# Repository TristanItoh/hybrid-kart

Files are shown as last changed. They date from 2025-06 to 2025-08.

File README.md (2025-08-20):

# The Hybrid Truck Kart
A custom hybrid truck-style go-kart with a 49cc 2-stroke engine, a cargo bed, and 400w 36v hoverboard motors and batteries, all on a custom built frame.

## Why?
I've dreamed of building a go-kart for a while now, but the high cost of parts always held me back. This project is my first step to building my end-goal project: a full sized hybrid vehicle. It's sort of like a practice demo for making vehicles, while still making something cool that I can drive around in. <br/> *But why a truck?* To carry around my treasure!

## Technical Overview
This go-kart is a hybrid system:
- **Powertrain**: A 49cc 2-stroke 3hp engine drives the rear axle via a 14T/54T sprocket setup, with two hoverboard motors on the front wheels providing acceleration, controlled by 400W BLDC controllers.
- **Frame**: Custom made with salvaged steel tubes, cut to the right lengths, with steel rods as axles
- **Electronics**: Repurposed hoverboard batteries and 400w 36v motors, integrating them into this go-kart instead.
- **Challenges**: Hybrid powertrain, frame stability with heavy loads, and designing a steering system.





## Wiring Diagram
wire diagram go kart

## BOM for Hybrid Truck Kart

| Item | Description | Quantity | Source | Estimated Cost |
|---|---|---|---|---|
| Steering Wheel | 3D Printed | 1 | 3D Printer | $3.00 |
| Engine | 2 Stroke 49CC 3HP | 1 | Aliexpress | $55.00 |
| Sprocket & Chain | 54T T8F | 1 | Aliexpress | $13.51 |
| Fuel Filter + Tubing  | | 1 | Aliexpress | $8.00 |
| Throttle | Foot Pedal | 1 | Aliexpress | $9.21 |
| Hoverboard Motors | Wheels w/ hub motors pulled from used hoverboards| 2 | Already Have | $0.00 |
| Metal Tubes | Metal for vehicle frame | 1 | Already Have | $0.00 |
| Metal Plates | Vehicle flooring | 1 | Already Have | $0.00 |
| Batteries & Electronics| Pulled from used hoverboards, specs unknown | 2 | Already Have | $0.00 |
| BLDC Electric Motor Controller | 2PCS DC 6-60V 400W BLDC Three-Phase Brushless Motor Controller PWM | 1 | Amazon | $25.00 |
| Hole Saw Kit | Includes some hole saws we need, better value | 1 | Amazon | $36.00 |
| Bearings | 10 Pack 3/4" ID 1-3/8" OD | 1 | Amazon | $14.40 |
| Wheels | 10" pneumatic wheels | 2 | Harbor Freight| $20.00 |
| Plywood | 1/2" 2x4s | 2 | Home Depot | $38.00 |
| Steel Rod | 3/4" 48 in. (cut to be about 28 in.) | 1 | Home Depot | $34.86 |
| Chair | Plastic folding chair, cut down to use as real chair | 1 | Home Depot | $26.00 |
| Steering Rod | Long rod attached to steering wheel | 1 | Home Depot | $15.46 |
| Chain Breaker Tool | | 1 | Walmart | $9.96 |
| Miscellaneous | Screws, washers, bolts, nuts, fuse | Various  | Whatever | $15.00 |

**Total Estimated Cost: $323.40**

## Finished Build + Demo

Here's how the finished kart looks:



And a video of it working:
https://youtu.be/AjNEpxWg-Ms

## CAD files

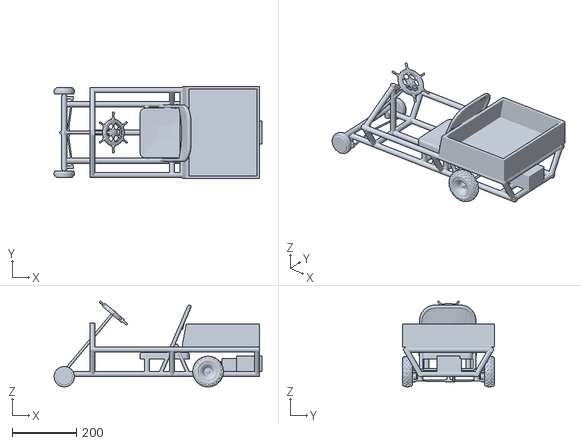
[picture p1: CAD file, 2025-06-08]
CAD/Hybrid Truck Kart.stl
648.6 x 288.3 x 267.9

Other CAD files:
CAD/Hybrid Truck Kart.obj

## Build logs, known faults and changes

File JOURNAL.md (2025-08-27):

---
title: "Hybrid Truck Kart"
author: "Tristan Itoh"
description: "A hybrid go kart truck"
created_at: "2024-06-06"
---
### Total Time Spent: ~15 Hours
# Journal

## Day 1 - June 6
Brainstorming what parts to use:
- Engine: either a cheap aliexpress engine, or a predator 212 if budget allows
- Motors: either cheap hoverboard motors, or a good one like an my1020

(The more expensive ones would obviously be better, but I'll see how much everything ends up costing in the end)
- Metal will likely be random scrap metal I have around, or some from metal recycling. Not too sure where to get metal.
- Wheels are pretty good and cheap at harbor freight
-   Or can possibly use the hoverboard wheels
- Not sure where to get parts for steering mechanism

I've created a rough model of the go kart:


I tried to keep it simple while still keeping it professional.<br>
And I kind of kept adding stuff to it as I made it. At first it was just a super basic frame. Then I turned it into a truck. Then when doing the steering wheel I added the elevated beams on both sides. The result turned out pretty cool.
### Total Session Time: 3 Hours

## Day 2 - June 7
Today was focused on figuring out what parts to use and creating the BOM. I had a rough idea when designing the CAD model, but only for things like the wheels, engine, and motors. For smaller stuff I had to spend quite a while thinking about it.<br>
A few notable parts:
- **Steering wheel and seat:** I tried look for cheap parts for both of these but all of them ended up way too expensive. Nobody is paying $30 for a plastic steering wheel. I opted to 3D print the steering wheel myself and buy a plastic folding chair for the seat. Folding chair is a little rough, cause I'm gonna have to cut the legs off to make it actually fit well.
- **Sprocket and chain:** This was probably the hardest parts to find. Since the engine is this cheap chinese one from aliexpress, it needed a specific type of sprocket that would still fit on our rear axle. For this itself, it probably took around an hour to find.
- **Motor controller:** Finding a good motor controller was harder than expected. I was planning to use one of those box ones with wires sticking out, but after getting feedback from soneone in the Hack Club slack, I found out about BLDC controllers which I ended up using.
- **Bearings:** The tough part about bearings is that I needed a specific inner diameter *and* outer diameter. It was easy to find one or the other, but not both. The only place I was able to find both was on a specific site for bearings, but it was $5 for each one. I don't think Highway would like that very much so i opted for some cheap bearings on Amazon that arent the exact size, but close enough.


The total price of the kart ended up at just over $300. It's a little more than I was expecting, but it is lower than the $350 at least. That's if I can even get this accepted as a 10 point project...<br>

I also spent some time refining the CAD model. The previous version was the right design but wrong proportion. It was far too big, so I shrunk it down. I also found that in the shrunken down version, it was only about 2 ft wide, so I ended up also having to make it wider and also make it a little longer. A couple more changes too, like the sprocket and chain, steering wheel model, and wheels.


### Total Session Time: 6 Hours

## Day 3 - June 8
Since the CAD model and BOM are pretty much done, I spent today refining both of those, as well as looking for some parts to buy.<br>
### CAD Changes
Originally I was planning to build the seat of the go kart from scratch out of wood, but decided it would only cost a little more to just get a standard foldable chair. Although I already decided this yesterday, I didn't update the CAD model accordingly, so I found a chair 3d model, stuck it on the car model, and chopped its legs off to where its much closer to the ground


### BOM Changes
After double checking each of the links on the BOM, it turns out the hole saw kit didn't have a 1-3/8" saw, which we definitely needed. I had to look for a different one that did have it, and this new one has many more sizes but it's like $10 more. Hopefully Hack Club won't mind, because I kind of need them and buying them individually would feel like a waste.<br>
I also added a throttle to the BOM that I will use to control the hoverboard motors.
### Finding Parts
I'm guessing we're supposed to wait for the grant before buying any parts, but I'm going to buy some now and hopefully get it reimbursed later. First I wanted to get the two metal rods I need, one for the rear axle, and one for the steering. I picked up the steering axle at a Home Depot, but they didn't have the axle rod I needed. So I ended up having to go to a different much larger home depot to get it. I also looked for hole saws at both but they are way too expensive. I also picked up some washers that I'll need.
<br><br>
Oh yeah, and I finished most of the README file. Should be able to submit this whole project soon 👍
### Total Session Time: 6 Hours

## Day 4 - June 9
Today was fairly short. I fixed one thing and submitted the project. <br>

I posted my project in highway-pitstop and it seems to be getting positive reactions. One person replied on it and said it would be helpful to know more specifics about the hoverboard motor. After seeing that I tried to find the exact model (which i couldnt find last time a tried) and I did end up finding it this time. It ended up being 400 watts instead of the expected 350 watts. It was an easy fix though, the same motor controller i picked also has a 400w version. The go kart should be nearly perfect now.

## Day 8 - June 13
So two days before, alexren replied to my project and pretty much has concerns about if I can finish the project on time. I do believe i can so i replied, but it seems like alex hasn't really seen any replies.<br>

Then yesterday, I decided to just start working on the project anyways regardless of if it gets accepted or not. Maybe even just starting it now can prove that i will finish it on time. I've had all my metal lying on a glass table covered in tools and it was all kinda dirty. I basically spent the whole day cleaning it all up and moving it all into the garage so i can start working there.<br>

And now finally, today, I started doing real work, starting with learning to weld. I tried welding two pieces together but it didn't really work. Then I tried with something else that's a little bigger and it actually worked. But when i tried to weld something for a third time... my whole table shattered.<br>

I guess I should have expected that from welding on a glass table... But tomorrow i'll buy a welding blanket and start welding on a plastic table instead
### Total Session TIme: 4 Hours

## Day 12 - June 17
For the past few days, I've just continued practice welding. I remember a day or two ago I kept trying to weld 2 pipes together, and it just kept snapping apart. But I bought new electrodes and they work like magic. Those 2 pipes I probably still have to grind down the excess, but I tried on 2 new ones and they are now solidly attached. Now I've basically got 2 long steel pipes, which I'll use for the two sides of the bottom part of the frame. Tomorrow I'll start cutting the ones that go in between, and maybe even weld them.

## Day 15 - June 20
I've kind of wasted the past day and a half trying to get the engine to work. I swear it's like I tried everything. New gas, starter fluid, starting it manually, still nothing. I guess all I really did those past 2 days was weld 2 more pipes together. Now I've got 3 of these long pipes. Today I finally caved and bought a new engine. 

s-l1200

It's a predator 212. I don't think I would have bought it if there wasn't a sale on it. I got it for $120 which is pretty pricey, but it's not bad considering its like double the power for double the price. I successfully got it to run, and it was so much easier to start then the Aliexpress one. Just fill it up, flick a thingy, and pull.<br> There are three problems though:
  1. It doesn't have a clutch
  2. It's pretty big
  3. The sprocket I bought will no longer be compatible<br>

For the clutch, I can easily buy one from Amazon to put on it. I've been looking for new sprockets and another concern is if the gear ratio will be enough. I could probably just return the other sprocket I bought for the previous engine. And for the size, I'm not sure. I might just have to raise the bed even higher, and put a hole in it for the gas.

## Day 22 - June 27
So uhh i've kind of forgotten about this whole journaling thing. But I have certainly been working. I'll kind of split it into parts:

### Plan:
I've kind of split this whole project into 6 parts. Here are they:
1. Design [COMPLETED]
2. Trial and error, buying parts and tools [COMPLETED]
3. Cut pipes [COMPLETED]
4. Cut holes in pipes [DOING]
5. Weld pipes together, complete frame
6. Install everything onto frame

### Trial and error
There's been a lot of random stuff ive had to buy for this project. First I bought a drill press to drill holes into pipes easier. But just holding pipes under it is too unstable, so I decided i needed a pipe notcher too to hold it in place. So I bought some random pipe notcher from offerup. It was crazy nasty so I had to clean it up. And then I realized my drill doesnt fit the shaft. So I tried putting it on the drill press instead, but it just wouldn't stay on steady. And then that one kind of broke, so I bought a brand new pipe notcher. And even that one didn't work. So i kind of had to give up with the drill press and instead do a regular drill. So i then had to buy an entire new drill with a bigger shaft and yeah... Yap over.

### Design
So I've already designed the model but i wanted to clearly have what pipes im using for what parts, how to cut them up, and basically just all the information i'll need to assemble the frame. Here's some examples:
iawdmage
imaawdawge

### Cutting pipes
So after all the trial and error, I finally started cutting the pipes. For now just with the angle grinder and not with the hole saw. I think it took like 3 days to cut them all, and that was after all the trial and error, which kind of ate up a lot of time. There wasn't really anything notable, just a bunch of straight cuts. Designing everything out beforehand was super handy. I could easily see what to cut, so all I had to do was measure, draw a line, and go for it.

## June 28 to July 9 (Going to stop counting days)
With all of the straight cuts out of the way, I can move forward with doing all of the tube cuts with the pipe notcher. 



### The super cool pipe notcher process!!!!!!
So I thought this would be pretty straightforward. I have my pipes, pipe notcher, and thread cutting lubricant. It was a little trickier than I thought. Basically my initial strategy was this:
- Mark a dot at the edge of a circle I needed to cut
- Insert into pipe notcher, making sure it's straight if there's another hole it needs to be parallel to
- Apply lubricant, set drill down into it, start drilling
- Drill until either hole saw gets stuck in pipe or there's a bunch of smoke
- In either scenario, apply more lubricant and continue drilling again

This strategy did seem to work for like the first 1/3 of the holes I needed to cut. But I sort of refined the process cause it was inefficient at times and even dangerous. Here are changes I made along the way and why:
1. Draw a full arc around where I need to cut - this way I won't have to keep checking the design for which side of the circle the dot is on
2. Instead of resting the drill on the pipe, then starting to drill, instead keep the drill spinning full speed THEN put it into the pipe - pretty obvious, digs into the pipe way easier at the start. idk why i didn't think of this at first
3. MOST IMPORTANT attaching the pipe notcher to the table - this one might seem strange, but it actually made it so much safer to use. Sometimes the hole saw would get stuck with the pipe, and it would then spin the entire pipe notcher around, either hitting me or falling off the table (or both). After I got a couple cuts from this happening, I finally just bolted it down to the table.

After making these changes, the process went a lot smoother.

### More cuts

Now that the pipe notcher process was refined, I began to drill the rest of the easy holes (as in the ones that are on long pipes that are just centered in the middle). This did take longer than it should have, mainly because I began to spend more time on my Open Sauce project that I was gonna need to finish soon. So after like a couple days, all of the straight holes were cut, now there were the more complex ones. For holes that were centered at the edge of a pipe (so that there's only half a circle being cut into them), I had to sort of offset the shaft that the drill is attached to, so that it was no longer centered in the middle of the pipe. Then there were some short pipes that weren't long enough to be held in the pipe notcher. This was pretty hard to figure out, and I thought I was just gonna have to do it the hard way with a drill press. But I found that if i stuck it in, then just put another pipe locked into it to where they're touching and basically just stuck together, it basically works as if it was just one long pipe. And with the short pipes cut, I could finally move forward to the fun part - actually welding everything together!!!!!

I feel like it might seem I didn't do a whole lot in this time, but as my excuse, I really had to lock in on a project for Open Sauce and had less time to spare on this project.



## Note: From July 10 to July 21, I was in San Francisco for Undercity and Open Sauce! Just want to make sure you don't think I was doing nothing for nearly 2 weeks lol.

## July 22 - Starting Welding
With Undercity and Open Sauce out of the way, I could finally put my full efforts into this project. I started right away with welding together all of the metal I've already cut. This was probably my favorite part. Before welding, it still looked like I had nothing done. But just starting to weld stuff together, the whole thing just starts coming together. I welded in layers sort of, starting with first, the very bottom. It's funny, even though the bottom should be the strongest, I welded it first where my welds were not great. This was the very first part I welded:

imaawdawdge0

You can probably see how I used the hole saw to cut circles into both ends of the pipe. The top has that crescent curve, and the bottom does too, already welded together to the longer pipe at the bottom. That short piece is the back piece of the bottom. Next, I would weld the other side on:

imagawdwade0

In this photo, that one side isn't welded on yet, but you can now more obviously see it's the bottom of a go kart. In the previous photo with just one side, I managed to do it very straight (as in like perpendicular) and it turned out really nice. For this second one, though, it didn't go so smooth. At first I tried welding it on very straight, then I burned a very large hole through the side, so I then had to flip it over and weld on a clean side. Little did I know, when I flipped it over, the previous weld that stuck out made it so that it was no longer straight. I didn't really notice until I stood up after I finished welding. Honestly I thought i was gonna have to grind it off and reweld, but it was able to bend a little... very forgiving.

## July 23 to July 31 - Completing Welding

At this point (July 23) school started up again. Let's just say it ate up a little bit of time that I could be spending on this project. For the next week or so, I was kind of locked in, didn't take any pictures or anything, just straight up welding every night. You'll definitely see how it came along a lot better in the August 1 log, but I'll still try to describe it here. I pretty much finished the entire frame, which includes:
- 3 more bars between the sides on the bottom
- 6 slanted vertical bars holding up the upper layer of the frame
- The upper layer of the frame, held up by the vertical pieces
- 4 little legs for the chair to rest on and keep it more elevated

I don't remember every detail of what I worked on, so I'll just give little snippets of notable parts:

1. When continuing the bottom layer from July 22, I found out I could just bend the bent side out to fit a new bar in the front that goes in between them. It was kinda scary cause I didn't know how well the weld would hold up. But it ended up being fine! And I could insert it very smoothly
2. Now an extension to the last thing, I then had to insert two more bars between the sides of the bottom that support the seat. I should have probably realized that I should weld the inner ones before the outer ones, but didn't really think of that. Conveniently though, I didn't have to bend it too much to get it to fit. If i wasn't able to get it in, I would have had to cut it slightly shorter, redo the holes, and then it wouldnt even be as tight, so very glad it worked out!
3. I planned to assemble the whole top layer before doing the vertical parts that bridge them together, but it didn't work out too well. When kind of just laying it out on the floor, I realized that I must have either measured the back wrong, or I just got the number wrong when I was making it in CAD, because it was like exactly 2 inches longer than it was supposed to do. At first I was worried i was gonna have to cut the whole back to be shorter, but I realized, I could just make those pieces on the sides of the top that curve outwards just go up instead. Then I can technically make the back as wide as I need. If I didn't realize this mistake, I would have the entire top layer too long and honestly... idk what I would have done.
4. Following up the last one, now when I wanted to figure out how the kart should go, I basically assembled it all just loosely, relying on all of them going through the holes to hold itself together. It held together nicely, all I had to do was make sure the vertical pieces weren't leaning torwards a side. Now that I could actually see how it will all go together now, all of the vertical pieces were at the perfect angles that I can weld them at, so I started welding those first. After like 1 or 2 of them being welded, It was pretty solid. The top part was staying on nicely (although it wasn't welded on yet), and after that pretty much all I had to do was just weld everything together in the same way I already had it arranged.
5. A design choice that differs from my original design was instead of having a tall triangle that holds the steering wheel, its just a simple horizontal bar that goes across. Honestly I don't really know which option was better structurally, but just in terms of finishing the project, the whole triangle thing was just unnecessary. In the image below, I put red lines that show where the new bar would go. The two pieces higher up that form a triangle will just be forgotten.



imaawdge0
(brother for scale)

## August 1 to August 3 - Creating Rear Axle and Setting Up Engine

Now, school was really picking up. With a week left for this project, that did not help. The work I did these next two days was not much, but it was something. 
### Engine mounts
First, I installed two bars that go across the right side of the bottom of the frame. This was where the engine would be mounted to. Same deal with the rest of the pipes, just measure, cut, weld. I actually put the two bars on the wrong side. When I realized the original plans had them on the other side, I thought I really screwed up. Very conveniently, though, if I were to put the engine on the other side, it would spin backwards. You can't really switch the direction the engine spins, so this accident was a lifesaver. Also something I forgot to mention earlier, since the engine shaft just spins continuously, I had to buy and install a clutch so that I can control it.
### Rear Axle
Next, I started working on the rear axle so that the engine can spin the wheels. I had to weld another pipe where the axle would go. Here, I could install bearings into each end of the pipe. I didn't have to weld them because it was already tight (it was hard enough just to cram them in lol). Then I was able to slide the rod into the bearings, probably the most satisfying part in a while. I could just spin and spin it around and it was so smooth. 
### Wheel Adapters
Meanwhile, I've been printing two adapters to attach my wheels to the axle. I designed it so that if I pop out the center part of the wheel, and make the hole inside a tight fit with the axle, it will securely attach the wheels to the axle. I got these pieces, crammed them into the wheels, then with the axle I just attached, I could then cram those wheels with the adapters onto the axle. This pretty much sealed the deal for the back axle and made it ready for the engine.

imawdaawdge0
imawadawdge0

## August 4 to August 6 - All the Engine Stuff

This is pretty much building upon what I did in the last log. In preparation of the chain and sprocket, I mounted the engine to the two bars I was talking about before by bolting it down. Next I needed to start working on the sprocket.
### Sprocket
The sprocket I bought on Amazon had a hole in the center that is way too big for the axle. I had to sort of come up with my own DIY solution. For this, I cut two square pieces of metal from this random elevator lift I had lying around. I could then weld those onto each side of the sprocket to patch the holes. And finally, I could drill a hole in the middle to fit the proper size. I was afraid that I was gonna screw up the hole and not keep it centered, but it turned out fine. This was basically the new sprocket finished.

Now I slid the sprocket onto the rear axle and put it in a position aligned with the engine's shaft. I could roll the wheels around and see the sprocket spin, which was a very good sign. Now I had to figure out the chain.
### Chain
The chain that came with the sprocket was decent, but too long, and I didn't have a chain breaker tool. I consulted an expert (chatgpt) and found out I can kind of just force the pin out so I can take some links off. I elevated the chain a bit and kind of just hit it with a screwdriver until it finally worked. This took like an unusual amount of time cause I couldn't figure it out. But finally when I did it, I shortened it, put in the master link, and I was able to attach it between the sprocket and engine clutch. The chain pretty much finalized the main drivetrain of the kart.

I rolled the kart outside to test it. When I started the engine, it surprisingly (or maybe not so surprisingly) actually worked well. Now that this was all done, all that was left is the steering and electric system.

imagawdawde0
imageawfr0

## August 7 - Steering and Electric System

THIS IS THE FINAL STRETCH!!!!!

I gotta admit something. I didn't do the steering according to the plan. I had to make a last minute change, just because of how little time I had left. Instead of the whole real steering system, I decided I could just attach the front axle to a single pivot point in the middle, and just steer with my feet at the bottom. On the plus side, I could actually finish on time. On the down side, it's just not as cool. Gotta make some sacrifices. 
### Steering
I already had a front axle piece that I was planning to use for the original steering system, so I could just reuse this as the main piece. I did something similar with the back wheels, where I 3d printed some similar adapters (just different inner diameter) so that I could attach hoverboard wheels to the axle. Then with this full axle with the wheels on, I simply just drilled a hole through both that axle and the middle part of the bottom of the frame so I can attach them at a pivot. There's a threaded rod piece (that I was able to salvage from the rear axle) that holds them together, with some nuts on it making sure they wont slip apart. All this is pretty much the entire steering system. Simple yet still working.
### Electrical System
Now for the actual electric system, I pretty much forgot to journal any of it since its felt like a side thing from the rest of the go kart. I don't really remember when I was working on it (the majority was before Undercity) but it was pretty much already done. To summarize, I got the main pieces, two hoverboard wheels and a hoverboard battery, and additional stuff like the throttle and motor controllers. I followed my wiring diagram to get it all working, and it was pretty satisfying seeing how when I step on the pedal, the wheels speed up. I did have to switch the throttle from a pedal to like a motorcycle kind of throttle because the cheap pedal one still let some current through even with no force on it. With this whole electrical system made, I, again, attached those hoverboard wheels with adapters to the front axle. And I didn't really think through where the electronics would actually go. I ended up just taping it all to the side of the front and just left it hanging there. I was definitely rushing at this time because I only had like an hour left to submit.

imawdawdage0

You can see all the stuff I've been talking about here. The front axle is attached at one point with the threaded rod holding it together. The electrical system (including battery) are all just hanging on the side there. And I have the throttle that's not really attached to anything, it's just handheld. One last thing is, to actually control the speed of the engine, I definitely did not have time for an actual pedal. I just tied a string to it and attached it to the front, so that the speed is controlled by how much I pull it. It's kind of a janky control system, where you steer with feet, and use your hands for speed of both engine and electric motors. 

I didn't even really test the go kart until I really needed to record the demo video. I got my brother to drive it so that I could take the video from the outside. The electrical system was definitely weak. It was definitely doing something, but you had to give it a little boost for it to actually pick up. Once you use the engine, it's pretty much free driving. It was so cool to see my creation actually driving around, and the feet steering actually gave good control over it. 

## The Future

So this Highway version of the project is pretty cool, and it's already like a whole go kart made. There are just a few changes I still want to make to it in the future:
1. Actual steering - The original steering system with a steering wheel is just so cool. I really want to add that steering on eventually so it's like a real car
2. Suspension - Right now all the wheels are just directly attached. Some very simple suspension could definitely make the ride smoother. It is pretty bumpy when I ride it, and the engine makes it a lot shakier!
3. Polish - The whole kart in general looks a lot like a scrap car. It technically is... but I don't really want it to look like that. I need to find a better place to put all the electronics, a proper system for controlling engine speed, maybe even cleaning up the welds, and finally, even painting the whole thing.

For whoever's reading this, I hope you found this project interesting! I definitely enjoyed making it!
